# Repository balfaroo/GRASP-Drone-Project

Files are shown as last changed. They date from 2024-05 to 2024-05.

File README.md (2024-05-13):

Hello! This is the repository for the GRASP Drone project, a senior project from Princeton University that sought to develop a drone that can autonomously retrieve and dropoff objects. Here you can find the CAD files and code for the drone, which are all documented on the "Build guide.docx" file. Please read through that file, as it should summarize most of the components and steps you'll need to take to build off of the project.

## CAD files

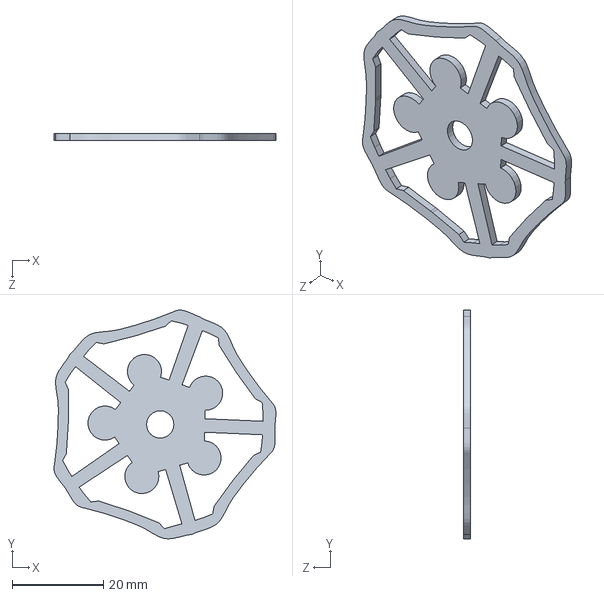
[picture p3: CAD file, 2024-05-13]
Mantis claw/4.SLDPRT
48.7 x 50.2 x 1.60 mm

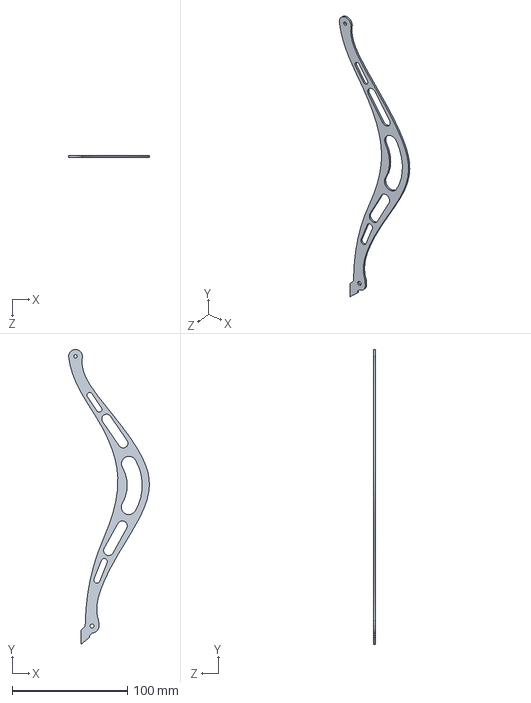
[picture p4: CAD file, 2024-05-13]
Mantis claw/1.fix.SLDPRT
70.1 x 256.0 x 1.60 mm

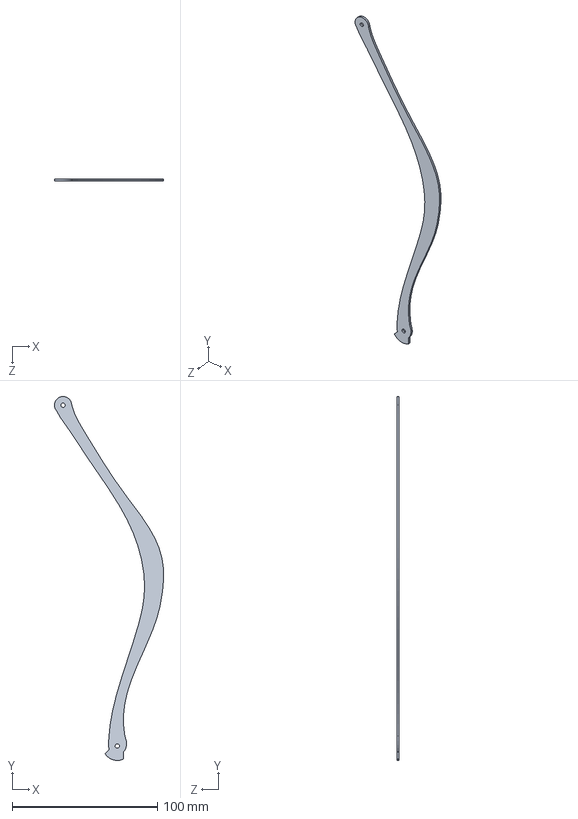
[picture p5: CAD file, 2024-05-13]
Mantis claw/2.fix.SLDPRT
75.3 x 251.0 x 1.60 mm

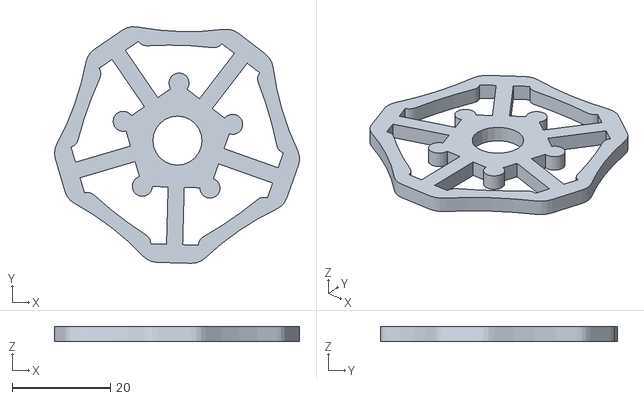
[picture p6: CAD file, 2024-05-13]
Mantis claw/STL files/Base_x2.stl
50.0 x 48.3 x 3.00

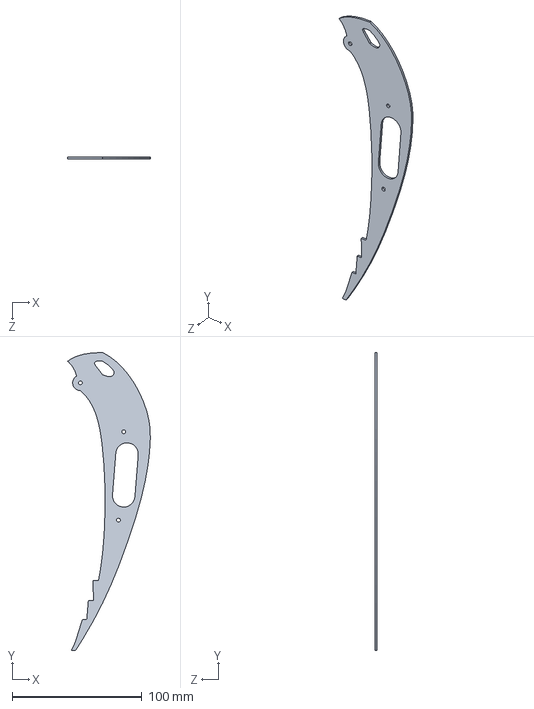
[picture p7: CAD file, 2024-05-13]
Mantis claw/3.fix.SLDPRT
63.8 x 230.0 x 1.60 mm

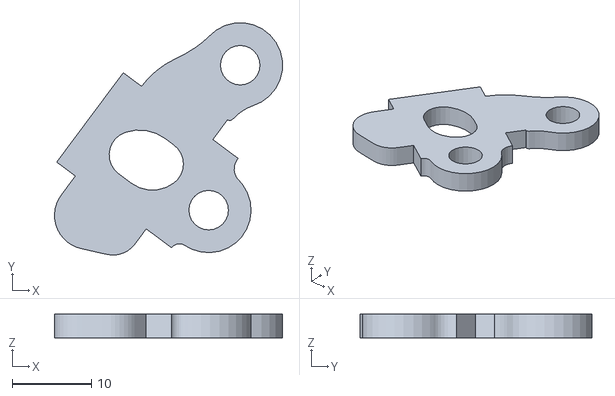
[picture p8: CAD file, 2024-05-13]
Mantis claw/STL files/Elbow_Joint_x10.stl
28.9 x 29.4 x 3.00

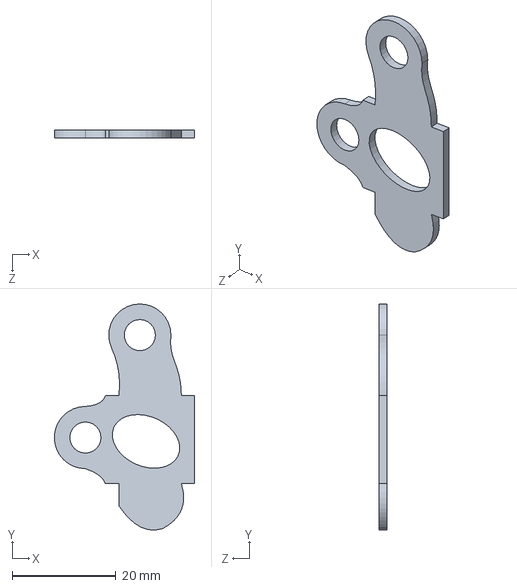
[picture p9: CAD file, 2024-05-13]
Mantis claw/5.SLDPRT
27.1 x 43.6 x 1.60 mm

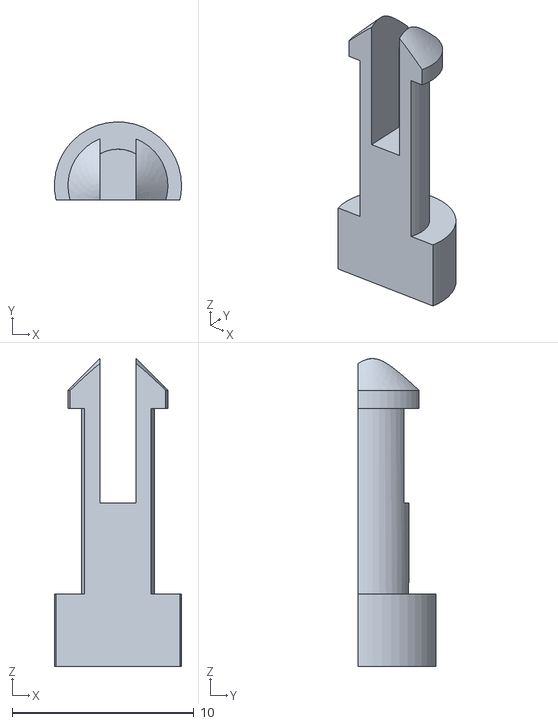
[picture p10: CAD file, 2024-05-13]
Mantis claw/STL files/mantis_claw_m4pin.stl
6.99 x 4.30 x 17.0

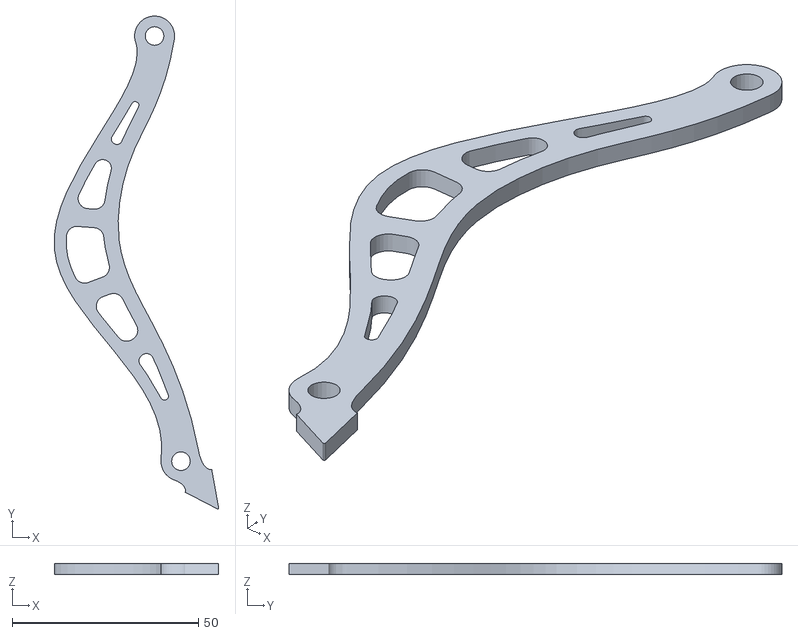
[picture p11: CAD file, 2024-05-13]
Mantis claw/STL files/Top_Arm_x5.stl
44.1 x 132.4 x 3.00

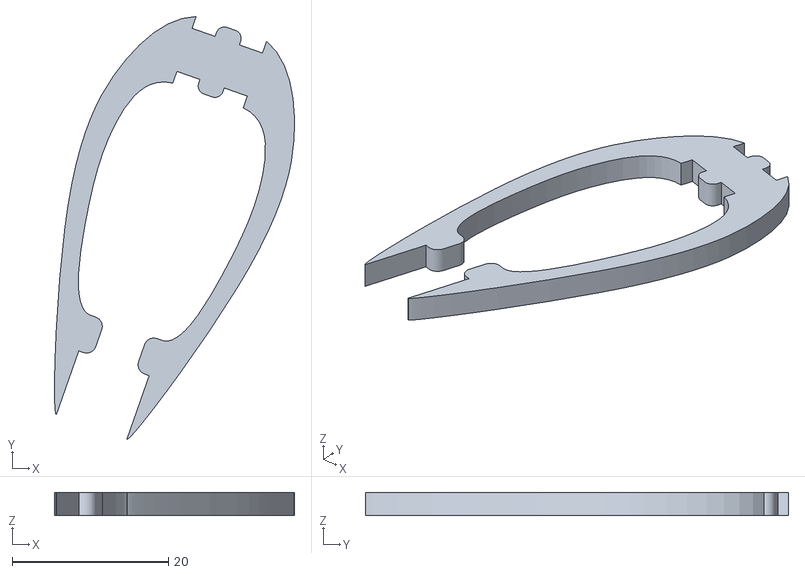
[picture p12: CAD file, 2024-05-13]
Mantis claw/STL files/Wish_Bone_x5.stl
30.7 x 54.2 x 3.00

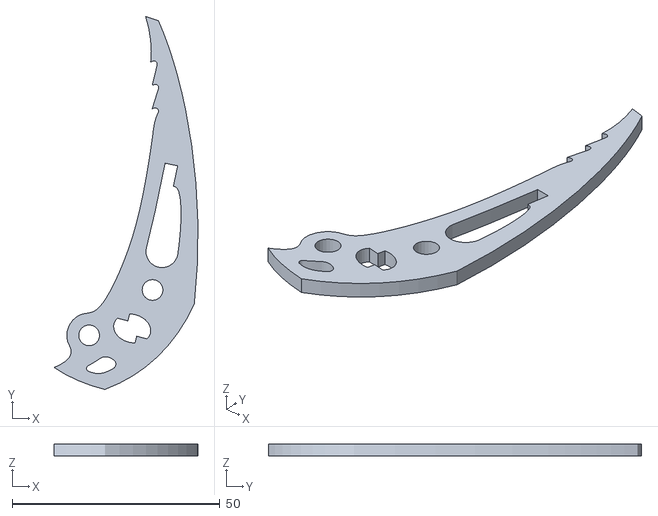
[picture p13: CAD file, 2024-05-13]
Mantis claw/STL files/Claw_x5.stl
34.6 x 89.8 x 3.00

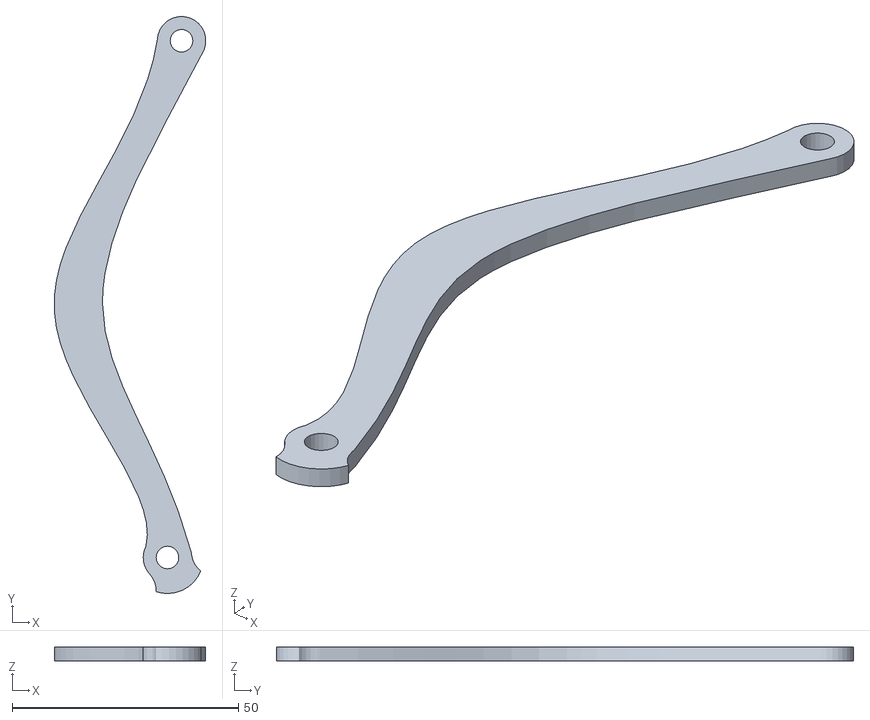
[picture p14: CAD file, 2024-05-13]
Mantis claw/STL files/Bot_Arm_x5.stl
33.5 x 127.7 x 3.00

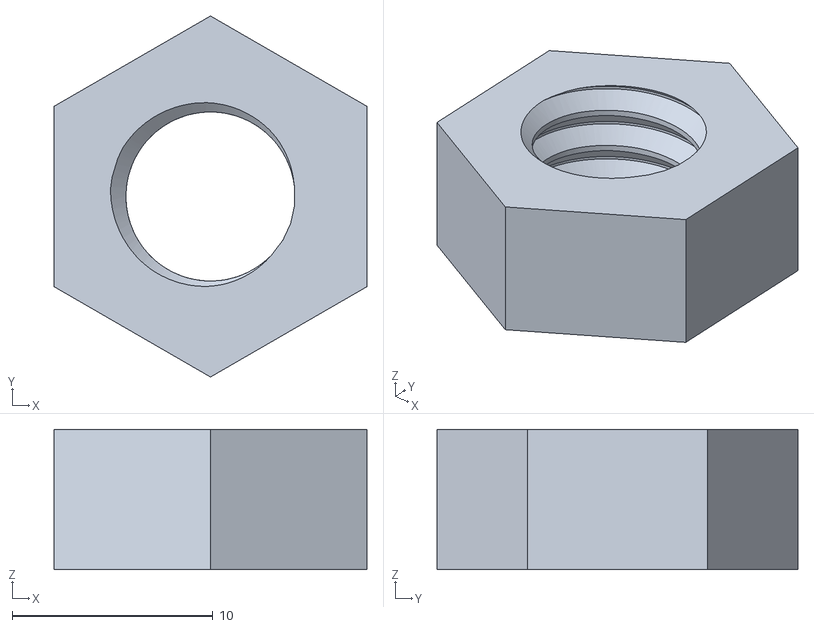
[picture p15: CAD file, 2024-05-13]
Mantis claw/STL files/Nut_M10.stl
15.6 x 18.0 x 7.00

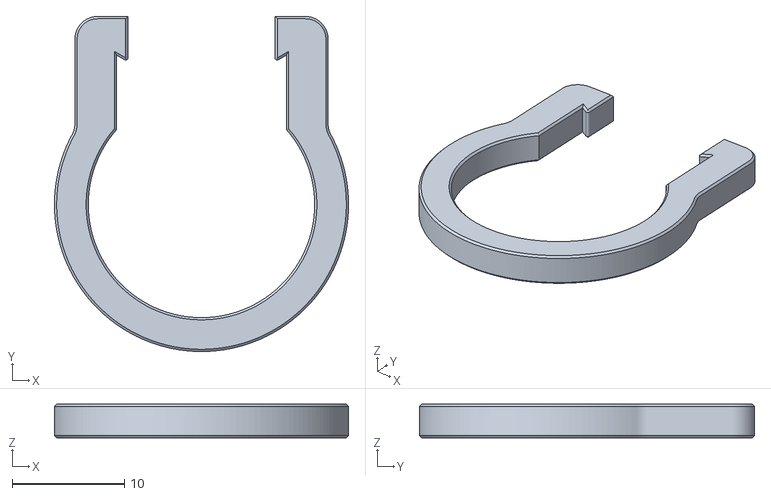
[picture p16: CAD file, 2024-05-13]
Mantis claw/STL files/eye_bolt_-_ring.stl
26.2 x 29.8 x 3.00

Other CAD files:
Mantis claw/STL files/eye_bolt_-_cap.stl
Mantis claw/STL files/Bolt_M10_40.stl

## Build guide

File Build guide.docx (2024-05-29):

# Overview

This document serves as a build guide for a drone used to perform autonomous pickup and dropoff of a small payload as described in our senior thesis (https://drive.google.com/file/d/1eyzDFhopvY5F14Urc1uSDVqPYYfMpOdw/view?usp=drive_link). The document will provide more information on the parts and assembly of the drone as well as the software setup to supplement the information presented in the thesis.

# Parts list

The following list contains all the off-the-shelf parts for the drone that we purchased:

- Holybro PX4 X500 V2 development kit (with Pixhawk 6X and 915 MHz radio) (https://holybro.com/products/px4-development-kit-x500-v2?variant=43018371629245)
- 8 GB Raspberry Pi 4 (https://vilros.com/products/raspberry-pi-4-model-b-8gb-ram?src=raspberrypi)
- Power distribution board (used to power RPi and servo motors) (https://www.amazon.com/Distribution-FCHUB-12S-Supports-Regulators-Current/dp/B07MHKTF7F/)
- 14.8 V LiPo battery (https://www.amazon.com/HRB-5000mAh-Connector-Airplane-Helicopter/dp/B06XK8WWX1)
- Servo motors (https://futabausa.com/product/rs303mr/)
- Radiomaster Controller (4in1) (https://holybro.myshopify.com/products/radiomaster-tx16s)
- Radiomaster receiver (https://holybro.myshopify.com/products/radiomaster-r81-receiver)
- Ark Flow optical flow sensor (https://arkelectron.com/product/ark-flow/)
- Arducam Wide Angle Fixed-Focus Camera Module 3 (https://www.arducam.com/product/12mp-imx708-usb-uvc-102-wide-angle-fixed-focus-camera-module-3/)
- GPIO pin cables (https://www.amazon.com/dp/B01EV70C78?psc=1&ref=ppx_yo2ov_dt_b_product_details)
- Screw terminals (https://www.amazon.com/dp/B07NSJV6NW?psc=1&ref=ppx_yo2ov_dt_b_product_details)
- XT30 plugs (https://www.amazon.com/gp/product/B0BKK5BGCR/ref=ppx_yo_dt_b_asin_title_o01_s00?ie=UTF8&psc=1)
- OAK D S2 RGBD Camera (https://shop.luxonis.com/products/oak-d-s2)*
- Intel RealSense d435i RGBD Camera (https://www.intelrealsense.com/depth-camera-d435i/)*

*Note: originally, we chose the RealSense camera to be our front facing camera. The RealSense has a dedicated software suite (https://www.intelrealsense.com/sdk-2/) for reading in information; however, trying to install this suite from the link on the Raspberry Pi is not possible. Instead, we had to follow these steps found in a GitHub thread (https://github.com/IntelRealSense/librealsense/issues/11506#issuecomment-1599168850) to build from source. The OAK D S2 does not have this issue, but we found that it is slightly slower than the RealSense. If you decide to use the RealSense, HolyBro sells a depth camera mount (https://holybro.com/products/depth-camera-mount?variant=42724474454205) that you can use to place the camera on the drone (this mount also has space to mount an optical flow sensor underneath it). If not, you will have to make your own mount, although we provide CAD files later in this build guide for some that we made.

# Build Guide

The X500 V2 kit that formed the base of the drone ships with instructions for assembling it. For more visual aids, PX4 contains a step-by-step tutorial with pictures (https://docs.px4.io/main/en/frames_multicopter/holybro_x500v2_pixhawk6c.html) (note that this guide is for a kit that uses the Pixhawk 6C, but the assembly instructions themselves are still the same regardless of if you use the 6C or 6X).

Once this base was built, we modified the drone by adding the 3D printed parts described in the next section.

In addition, we had to do some soldering to connect the power distribution board for the RPi and servos connected to the power distribution board for the drone. To do this, we soldered an XT30 male connector to the 8-60 V DC IN port on the distribution board. We then soldered a screw terminal on each of the GND and 5 V pairs on the board - one of these holds the pair of wires that powers the Raspberry Pi, and the other holds the pair that powers the servo motor (see notes on the potential improvements section). Once this is done, it can be mounted onto a 3D printed mount (CAD included in next section).

Once the Raspberry Pi is mounted onto the drone (using the mount that is described in the next section), it can be connected to the Pixhawk 6X in multiple ways as described on the PX4 documentation (https://docs.px4.io/main/en/companion_computer/pixhawk_companion.html) - ultimately, we used the Ethernet setup (https://docs.px4.io/main/en/advanced_config/ethernet_setup.html) (see more details in ROS2 bridge section).

# CAD for 3D printed parts

There are four CAD printed parts needed for assembling this drone: the mantis claw, RGB Camera Mount, Crossbar Mount for Claw and Servo Motor, and Depth Camera and Optical Flow Mount. All 3D printed parts are made of PLA with 50% infills.

Link to Claw STL: Files (https://drive.google.com/drive/folders/1if9A6Ysn8pVyYp9WaMxc0N_ZXBhwunZz?usp=drive_link)

Links to Mounts: Files (https://drive.google.com/drive/folders/1IK8oUzaypBWdTEbn7lTK5G9DpVHtkovL?usp=drive_link)

a. The Claw: The mantis claw is composed of several different STL files, including claw pins, bolt cap, bolt, bolt nut, bot base, gripper claws, top bot arm, bottom bot arm, arm joints, and gripper claw joints. For assembly, you need to 3D print 40 claw pins (redundancy included in number), 1 bolt cap, 1 bolt, 1 bolt nut, 2 bot base, 10 gripper claws, 5 top bot arm, 5 bottom bot arm, 10 arm joints, and 5 gripper claw joints. A tutorial to make the mantis claw can be found here: Tutorial (https://www.youtube.com/watch?v=yaddRVDZMao). When printing the STL files, it is important to scale each part down to 70% of its original size in order to take into account the limited space available underneath the drone body. Credit to Mantis Engineering Team for the claw idea.
b. RGB Camera Mount: The RGB camera mount can simply be downloaded from the CAD file and can be printed as is. The RGB Camera Mount will attach to the Crossbar Mount via a friction fit indent already added to the CAD files.
c. Crossbar Mount for Claw and Servo Motor: The Crossbar Mount for Claw and Servo Motor can simply be downloaded from the CAD file and can be printed as is; it is snapped onto the drone landing gears via a friction fit.
d. Depth Camera and Optical Flow Mount: The Depth Camera and Optical Flow Mount can simply be downloaded from the CAD file and can be printed as is; it is attached to the Platform board mounting rods on the drone body via a friction fit.
e. Raspberry Pi Mount: This mount can be attached to the payload board of the drone using 4 M2 screws and nuts (see reference picture (https://docs.px4.io/main/assets/payloads_x500v2.BlKS32-f.png)).

Once these are printed, the physical components can be added to their respective location. The Servo motor and Arducam RGB Camera can be fitted into their respective mounts via a friction fit. The OAK D S2 Depth Camera and Ark Flow optical flow sensor must be attached to their respective locations via screws (M4 screw and M2 screw, respectively). The claw can be attached via adhesive to the bottom of the crossbar mount. The next step would be to connect each claw to the servo motor using nylon strings. Each nylon string was attached from the five gripper arms to a spool on a servo motor. In the servo default position, the strings are taut, but they are fastened in locations where an object would still be able to push on the bottom part of each leg, allowing it to get captured. The claws should be taut enough that when the servo is activated to rotate 90 degrees, the claw arms move upward. See Section 3 of the GRASP Senior Thesis for more specifics about the physical assembly, which can be found here: File (https://drive.google.com/file/d/1eyzDFhopvY5F14Urc1uSDVqPYYfMpOdw/view?usp=drive_link).

# Setup on QGC

QGroundControl (QGC) is a ground control station, which can be used to calibrate various drone sensors and modify parameters that impact how the drone flies. More information is available on the PX4 documentation (https://docs.px4.io/main/en/getting_started/px4_basic_concepts.html#ground-control-stations).

To set up and calibrate the Pixhawk flight controller on QGC, we followed the steps on the PX4 documentation pages for installing PX4 (https://docs.px4.io/main/en/config/firmware.html) and on the QGroundControl Website (https://docs.qgroundcontrol.com/master/en/qgc-user-guide/setup_view/setup_view.html).

Additionally, we had to change some parameters on QGC to allow the drone to use the Ark Flow sensor for state estimation. These steps are described here. (https://docs.px4.io/main/en/dronecan/ark_flow.html#ark-flow)

Besides any changes in QGC parameters performed in the previous two steps we also found that changing the following parameters helped us fly the drone:

- EKF2_RNG_CTRL: set this to enabled so that the range sensor on the Ark Flow is used for altitude estimation as well. Before setting this parameter, altitude estimation was only done using the barometer on the Pixhawk, which gave values that did not make sense (i.e., negative values).
- EKF2_HGT_REF: set this to Range sensor for the same reason as above (using the Ark Flow for altitude estimation).
- COM_OBL_RC_ACT: set this to Land mode so that if your drone loses connection to the offboard computer while it is flying in offboard mode it automatically lands.

# ROS2 bridge + code

For offboard control of the drone, we chose to use the ROS2 bridge. Instructions for setting this up on the Raspberry Pi are available on the PX4 website (https://docs.px4.io/main/en/ros/ros2_comm.html). Since the Pixhawk 6X comes with an Ethernet cable, we also followed the instructions for the companion computer Ethernet setup. (https://docs.px4.io/main/en/advanced_config/ethernet_setup.html)

After following these instructions, you should be able to connect the Raspberry Pi with the Pixhawk 6X by running the following commands in a terminal on the RPi:

sudo ifconfig eth0 192.168.0.1 ### this sets the IP address of the RPi Ethernet port to the needed value, need to do this every time
MicroXRCE udp4 -p 8888 ### start the client that connects the two computers

If the connection is successful, you should see the following output in the terminal where you ran these commands:

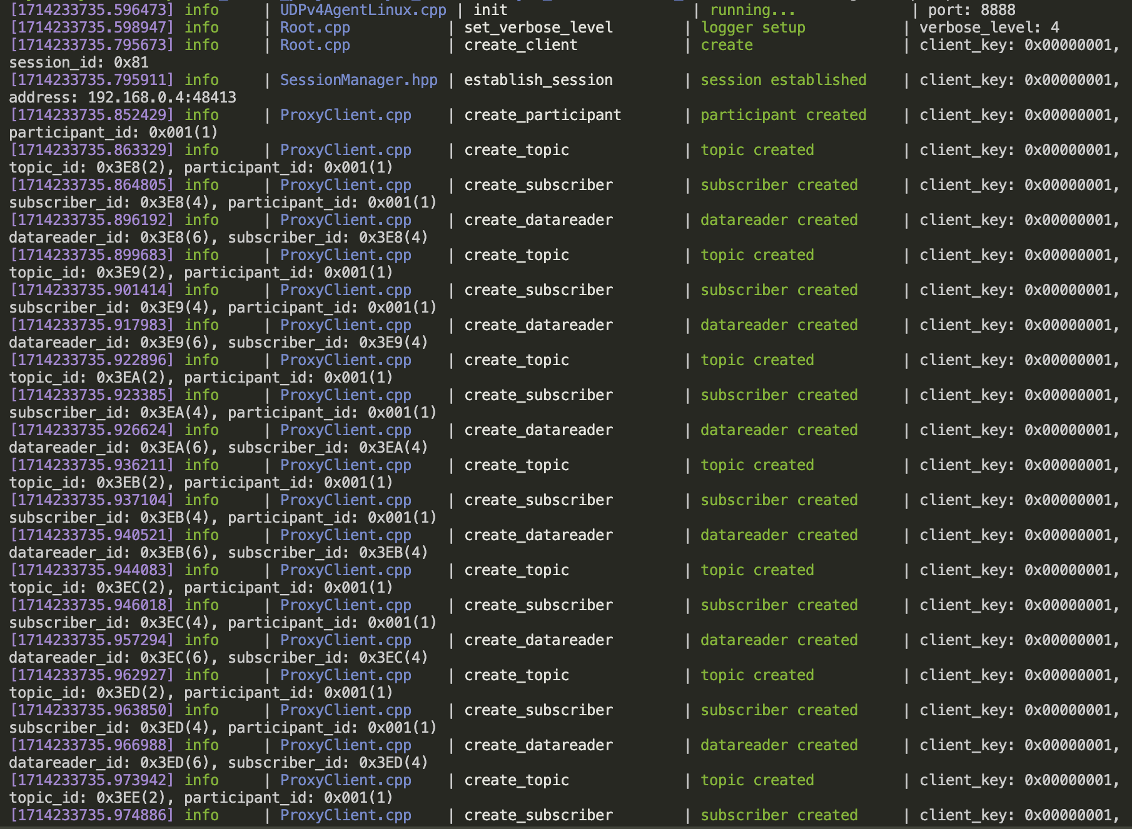
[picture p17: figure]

However, this connection can be very finicky (at least for us it was), and may sometimes not work on the first try, or may even disconnect in the middle of flying and testing the drone. If this happens, we found that simply running the commands a few more times until the connection initiates solves the problem. In rare situations, the connection would start up, but whenever we tried running our code to fly the drone, nothing would happen. When this happened, we found that running the offboard control example from PX4 (https://docs.px4.io/main/en/ros/ros2_offboard_control.html) first would solve the problem.

For control scripts, the GitHub repo this build guide is in contains the exact code used to control the drone, along with standalone Python scripts and Python scripts written for execution as a ROS2 node that were used for testing camera components. The main control scripts themselves are strongly based on PX4’s offboard control example (https://docs.px4.io/main/en/ros/ros2_offboard_control.html). In addition, we developed nodes that publish image information from the front-facing RGBD camera and bottom-facing RGB camera. Since we used AprilTags (https://april.eecs.umich.edu/software/apriltag) for object and destination localization, the topics that these nodes carry information about an AprilTag’s distance to a camera (for the RGBD only) and location within an image (both cameras). For ease of use, we also have provided several launch files that launch different combinations of the offboard control, bottom-facing camera, and front-facing camera nodes.

Finally, to control the servo motor that was used to open/close the claw, we wrote scripts located in the servo control folder (https://github.com/balfaroo/GRASP-Drone-Project/tree/main/offboard/offboard/servo_control) of the GitHub repo, which were developed following the instructions here (https://www.digikey.com/en/maker/tutorials/2021/how-to-control-servo-motors-with-a-raspberry-pi). These require admin access to run, and must therefore be run with sudo <file name>.py

# Tips for use + potential improvements

In this final section we want to give some pointers for making the drone easier to use and ways to improve the goal of this project.

1. Consider the lighting conditions when you test the drone. When we were performing our initial tests, we found that the drone would sometimes drift horizontally when it was supposed to hover in place. At first, we suspected that this was because the optical flow sensor was too close to the claw, and may have detected some of the natural movement of the individual claw legs that happens during flight, potentially leading it to erroneously detect horizontal movement. This caused us to shift the position of the sensor from behind the depth camera (as in the Holybro depth camera mount (https://holybro.com/products/depth-camera-mount?variant=42724474454205)) to directly underneath it. This caused us to mount the depth camera upside down to make room for the wire that connects to it (however, since we were not using the IMU on the camera it wouldn’t have a practical effect except needing to consider some negative signs when programming the drone). After further testing though, we found that the drift would only happen at night whenever the lights directly above the drone were on. By turning off these lights so that the testing area was only lit by lights that are adjacent to it, we were able to get rid of this drifting area.
2. You may notice that sometimes the motors of the drone do not begin spinning simultaneously when taking off. Usually this is a one-time issue that fixes itself if you stop the program running on the drone’s companion computer and restart it; however, if it persists, a likely solution is that you need to recalibrate the ESCs of the drone, which and be done on QGroundControl. Similarly, there may occasionally be a motor that “jitters” when flying, we were also able to fix this by recalibrating the ESCs.
3. For better performance of the grasping functionality for the drone, it may be worth experimenting with the following options:
  a. Consider changing the position of the bottom-facing camera to be directly inside the claw as opposed to being horizontally-offset.
  b. Similar to the above point, consider a new passive claw design that gives you more space to place the camera inside the claw, or
  c. Consider switching the design from a passive claw to an active claw.
4. Because of the need to run the servo motor control scripts with admin access, we were not able to incorporate this aspect into the ROS2 nodes, and instead executed the scripts manually based on output printed to the terminal from the offboard control nodes. This is because the nodes could not be run using the sudo command, since this would result in errors on the terminal we did not know how to work around. A potential solution to this would be to control the servo using the flight controller instead of the Raspberry Pi, since the 6X has auxiliary PWM ports that can be used for this purpose and can be set on QGroundControl. This is the initial method we wanted to use, and it seems that this would allow the servo to be controlled with ROS2 using the ActuatorServos (https://docs.px4.io/v1.14/en/msg_docs/ActuatorServos.html#actuatorservos-uorb-message) message, but we weren’t able to find a documented use of this and were unsure how to incorporate it. However, this would be a more elegant solution and is worth looking into.

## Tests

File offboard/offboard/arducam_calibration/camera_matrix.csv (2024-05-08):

9.976951689991706189e+02 | 0.000000000000000000e+00 | 3.706909466083776010e+02
0.000000000000000000e+00 | 9.295534157327572302e+02 | 6.416561442172160241e+02
0.000000000000000000e+00 | 0.000000000000000000e+00 | 1.000000000000000000e+00

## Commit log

2024-05-13 update with build guide + CAD
    [1.fix.SLDPRT, 2.fix.SLDPRT, 3.fix.SLDPRT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]
2024-05-29 Build guide includes servo control
